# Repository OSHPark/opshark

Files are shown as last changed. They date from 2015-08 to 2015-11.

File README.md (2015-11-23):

# LAN'd Shark Project
The LAN'd Shark is a small, wifi-connected shark robot with some wicked hair and underglow lights. This was built and designed by the Oshpark team for [PDX Mini-Maker Faire](https://www.omsi.edu/maker-faire-pdx) 2015. 

The shark communicates via an MQTT server, and has supplimental remote control boards that allow a direct interface. However, you could esily modify it for automated or automatic control. If you need a remote MQTT server, [data.sparkfun.com](https://data.sparkfun.com/) is simple and easy to use, or you can install your own with tools  such as [Mosquitto](http://mosquitto.org/).

## Project Status
### [BaseStation](basestation/)
The basestation is fully operational, and capable of reading up to 3 teensies, and transmitting data over a network to an MQTT server.

### [Controller](controller/)
The controller is fully operational in both hardware and code.

### [Shark Bot](sharkbot/)
The Shark Brains hardware is fully operational, and can drive several servo motors from an ESP2866. 

The chassis mechanics are still a bit undefined, and a bit erratic. However, the base board works great as a mounting platform for servo motors, and can be laser cut

The Arduino sketch is still in a bit of a mess, but can read incoming controller data and react. However, the Animation and ServoPlus libraries have some bugs and needs to be rewritten/updated in order for the shark to react correctly.

Here's a picture of the completed Sharkbot. 
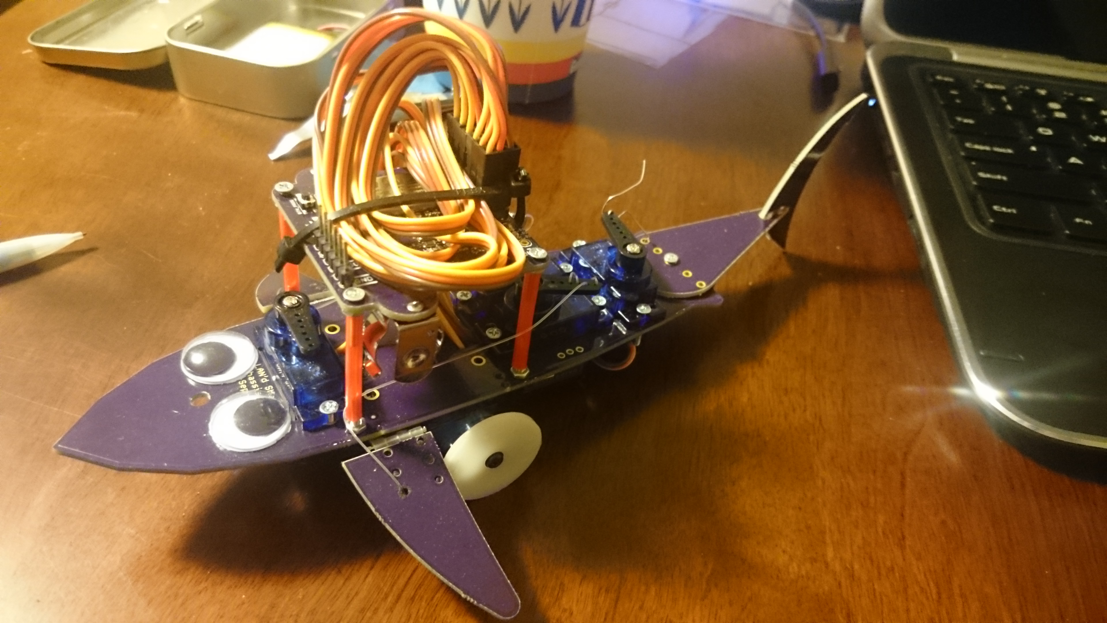
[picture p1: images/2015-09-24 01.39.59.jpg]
Shark posing


# Required Utilities
## Software
[Arduino 1.65](https://www.arduino.cc/en/Main/Software) 

[TeensyDuino](https://www.pjrc.com/teensy/td_download.html) if using the controllers

[ESP2866 Arduino](https://github.com/esp8266/Arduino) For the Sharkbot and basestation boards

[Eagle CAD](http://www.cadsoftusa.com/download-eagle/) is needed to modify the PCB files or generate gerbers. The `.BRD` files can be directly to [OSHPark.com](http://oshpark.com) for purchase without Eagle.

## Arduino Libraries
[PubSub Client](https://github.com/Imroy/pubsubclient)

[Teensy 3.1 SPI Slave library](https://github.com/soerup/Teensy-3.0-SPI-Master---Slave) for the controller boards

[Adafruit Neopixel (Teensy version)](https://github.com/PaulStoffregen/Adafruit_NeoPixel)

# Liscence 
Released currently under the [MIT License](./LICENSE.txt)

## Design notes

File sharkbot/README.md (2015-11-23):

# Sharkbot
This set of boards forms the mechanics of the roving LAN'd shark. It can be controlled via an MQTT server such as [Data.SparkFun.com](data.sparkfun.com), with either computer driven code or the companion [Controller](../controller/) and [BaseStation](../basestation/) boards. 

## Brains
This top board is the primary electronics, including the ESP chip and supporting programming components, voltage regulator, and LIPO battery monitoring. Also contains an output for a strand of Adafruit Neopixels

This board is entirely usable as a standalone servo controller. 
 
## Chassis and Fins
These boards contain the mechanics for sharklike actuation. The Chassis contains a strip of Neopixels for maximum gleefullness. 

If you don't need the neopixels, these boards can be exported as DXF or SVG and imported into most laser cutters or CNC software

# Software
This code uses the [ESP8266 Arduino](https://github.com/esp8266/Arduino) platform for the codebase. It also uses the Adafruit Neopixel library, which is conveniently included with the ESP Arduino downloads.

# Hardware

A very helpful resource was this tutorial for [creating a shark in maya](http://cgi.tutsplus.com/tutorials/create-a-realistic-shark-in-maya-using-subdivision-surfaces-part-3--cg-31246), even though I only used the 2d outline. 

The images in [references](./references) are copied from the tutorial for practical inclusion with the source files, and no claims are made to ownership. 

## BOM
See [BOM.txt](./BOM.txt) for the full component list from Eagle. Here's the notable/major components: 

- [ESP12E](https://www.adafruit.com/products/2491)
- Brains PCB. 
- Either Fin and Chassis  PCBs, or laser-cut equivilents (will have no place to mount neopixels)
- [Pair of AA Sized Lipo battery](https://www.sparkfun.com/products/7949)
- [MCP73871 LIPO battery management IC](http://www.digikey.com/product-detail/en/MCP73871-2CCI%2FML/MCP73871-2CCI%2FML-ND/1680971)
- [MC1703T 3.0V SOT23 Voltage ](http://www.digikey.com/product-detail/en/MCP1703T-3002E%2FCB/MCP1703T-3002E%2FCBCT-ND/1776944)
- [5x Neopixel LEDs](https://www.adafruit.com/products/1655)
- [5x Micro servos](http://www.hobbyking.com/hobbyking/store/__662__HXT900_Micro_Servo_1_6kg_0_12sec_9g.html). Various sizes and suppliers
- Several 2mm mounting screws, 3-6mm in length 
- 2mm nuts
- 2mm bolts
- Various passives and headers
- [Small nylon hinges](http://www.amazon.com/Du-Bro-Small-Nylon-Hinge-15-Pack/dp/B0006O4FYC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)

All passives use a universal footprint optimized for 0603, but tolerant of 0402 and 0805 components. 

# Errata/issues
The mechanics are not 100% defined, and some glue/creativity may be required to get this design fully operating. Our demo models were assembled with hot glue and some coffee stir sticks from 711.

There is no "off" button, which makes battery access critical as it's the only way to de-power the servo. The code implements a "sleep" function when the bootloader button is pressed, but this does not power down the servo motors.

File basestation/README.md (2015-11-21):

# BaseStation
This is an ESP2866 board that reads data from three [Teensy-based capacitive controllers](../controller/), and then sends it over wifi to an MQTT server to control a [shark bot](../sharkbot/).

## Simplified Wiring Schematic
Wiring the SPI bus requires 4 connections between the ESP and Teensy. 

```
  Controller                             BaseStation
  (Teensy 3.x)                           (ESP2866-12E)   
+--------------+                      +---------------+
|              |                      |               |
|           10 <------< CS <----------< Any IO        |
|              |                      |               |
|              |                      |               |
|           13 <------< SCK <---------< 14            |
|              |                      |               |
|              |                      |               |
|           11 >------> MISO >--------> 12            |
|              |                      |               |
|              |                      |               |
|           12 <------< MOSI <--------< 13            |
|              |                      |               |
+--------------+                      +---------------+
```

Other connections are simply there as part of the bootloading process.

# Known issues
Doesn't contain programming header of any sort, which makes changing wifi connections very difficult. Uploading firmware will require soldering to the ESP pads. 

It should be possible to configure the Base Station as a Wifi access point and run the MQTT server locally, in addition to handling the button input. However, this was not due due to time constraints and libraries available. 

# BOM
Only requires a few passive pull up/pull down resistors and an [ESP12E](https://www.adafruit.com/products/2491)

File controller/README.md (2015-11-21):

# Capacitive controller
This is a small Teensy 3.1 based board, which works as a 4 way direction pad with 2 buttons. The board provides a SPI interface, and the button presses can be picked up using a standard SPI Library.

# Usage 
Currently, this code only works when wired the BaseStation board. However, the Teensy is capable of operating as a USB human interface device, and with some tweaks to the code, the board can easily be used to operate a computer with capacitive buttons.

## Code requirements
Compiling the provided code requires a special [Teensy 3.1 SPI Slave library](https://github.com/soerup/Teensy-3.0-SPI-Master---Slave), as this functionality isn't provided by standard Arduino SPI libraries.

# BOM

- 1x [Teensy 3.x](https://www.pjrc.com/teensy/index.html). We're partial to the [purple ones](http://store.oshpark.com/products/teensy-3-1).
- 2x 14-pin male 0.1" headers
- 2x 14-pin female 0.1" headers

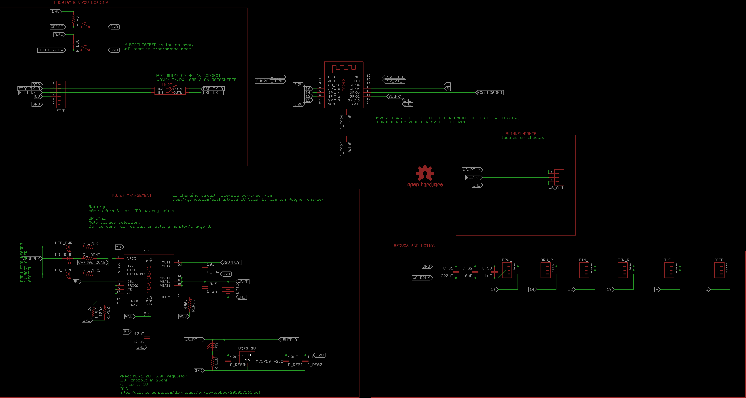
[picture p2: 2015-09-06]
sharkbot/eagle-files/brains.schematic.png

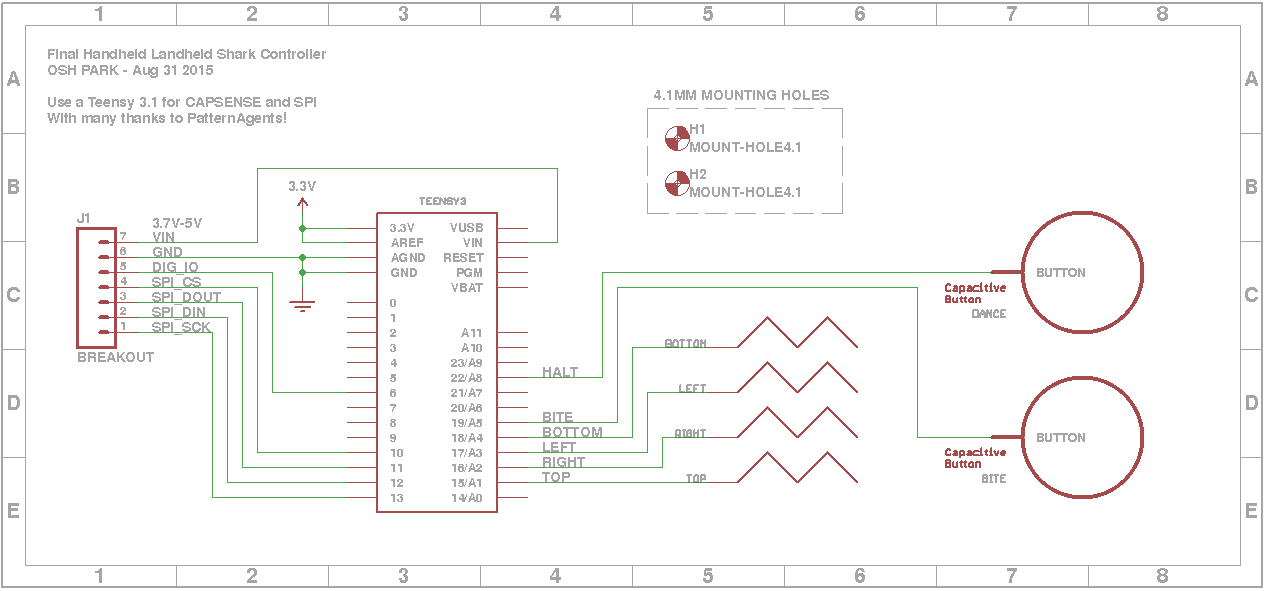
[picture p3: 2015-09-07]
controller/eagle-files/v3-schematic.png

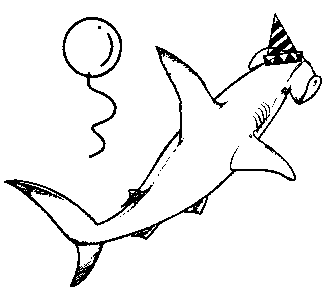
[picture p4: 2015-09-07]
controller/eagle-files/images/dance.bmp

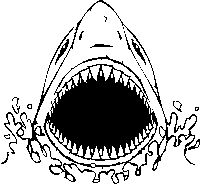
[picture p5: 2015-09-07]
controller/eagle-files/images/shark.bmp

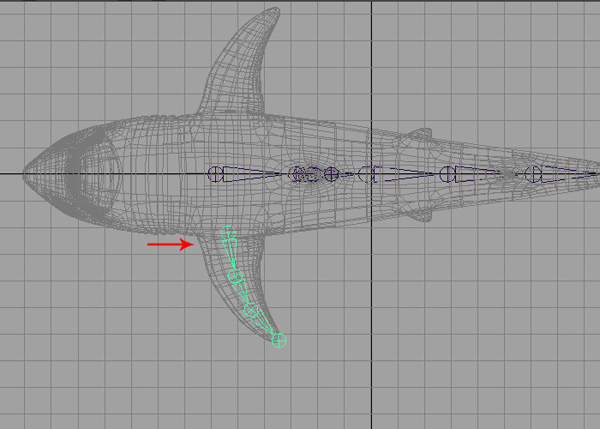
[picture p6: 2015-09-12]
sharkbot/references/Maya_Shark_PT3_11.jpg

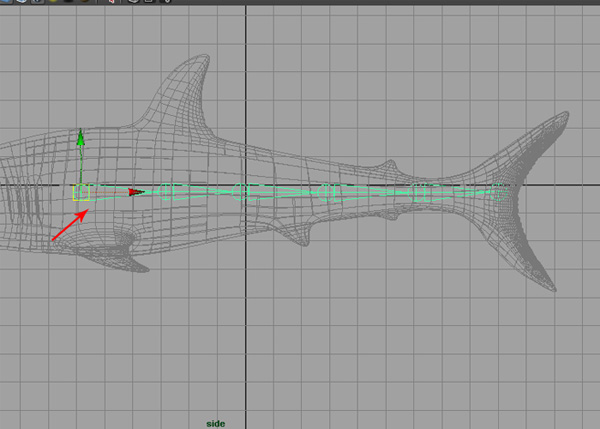
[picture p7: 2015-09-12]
sharkbot/references/Maya_Shark_PT3_6.jpg

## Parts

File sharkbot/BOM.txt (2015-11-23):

Partlist

Exported from brains.brd at 11/20/15 8:29 PM

EAGLE Version 7.3.0 Copyright (c) 1988-2015 CadSoft

Assembly variant: 

Part     Value             Package                  Library                    Position (mil)        Orientation

BAT2                       BATTERY-AA               SparkFun-Electromechanical (1000 1050)           MR270
BITE                       1X03_LOCK                SparkFun-Connectors        (1950 1420)           R0
BTN_PROG BUTTONPJRC        KMR432GLFS               tekdemo                    (740 1560)            R270
BTN_RST  BUTTONPJRC        KMR432GLFS               tekdemo                    (740 1200)            R270
C_5V     10uF              0402-0603-0805-UNIVERSAL tekdemo                    (1170 390)            R270
C_BAT    10uF              0402-0603-0805-UNIVERSAL tekdemo                    (1000 510)            R0
C_ESP1   1uF               0402-0603-0805-UNIVERSAL tekdemo                    (1880 1980)           R0
C_ESP2   0.1uF             0402-0603-0805-UNIVERSAL tekdemo                    (1880 2070)           R0
C_REG1   10uF              0402-0603-0805-UNIVERSAL tekdemo                    (1780 880)            R180
C_REG2   1uF               0402-0603-0805-UNIVERSAL tekdemo                    (1780 790)            R180
C_REGIN  10uF              0402-0603-0805-UNIVERSAL tekdemo                    (1780 570)            R0
C_S1     220uF             1210                     tekdemo                    (2090 750)            R180
C_S2     10uF              0402-0603-0805-UNIVERSAL tekdemo                    (2090 660)            R0
C_S3     .1uF              0402-0603-0805-UNIVERSAL tekdemo                    (2090 590)            R0
C_SUP    10uF              0402-0603-0805-UNIVERSAL tekdemo                    (1280 390)            R270
DRV_L                      1X03_LOCK                SparkFun-Connectors        (1950 890)            R0
DRV_R                      1X03_LOCK                SparkFun-Connectors        (1950 990)            R0
FIN_L                      1X03_LOCK                SparkFun-Connectors        (1950 1090)           R0
FIN_R                      1X03_LOCK                SparkFun-Connectors        (1950 1220)           R0
FTDI                       1X06_LOCK                SparkFun-Connectors        (660 970)             R270
IC_LIPO  MCP73871          QFN20                    adafruit                   (1180 630)            R180
LED                        0402-0603-0805-UNIVERSAL tekdemo                    (1490 390)            R270
LED_CHRG                   0402-0603-0805-UNIVERSAL tekdemo                    (1590 810)            R180
LED_DONE                   0402-0603-0805-UNIVERSAL tekdemo                    (1590 720)            R180
LED_PWR                    0402-0603-0805-UNIVERSAL tekdemo                    (1590 630)            R180
R_BOOT                     0402-0603-0805-UNIVERSAL tekdemo                    (950 880)             R180
R_LCHRG                    0402-0603-0805-UNIVERSAL tekdemo                    (1420 810)            R180
R_LDONE                    0402-0603-0805-UNIVERSAL tekdemo                    (1420 720)            R180
R_LED                      0402-0603-0805-UNIVERSAL tekdemo                    (1390 390)            R270
R_LPWR                     0402-0603-0805-UNIVERSAL tekdemo                    (1420 630)            R180
R_PD1    2k                0402-0603-0805-UNIVERSAL tekdemo                    (950 690)             R180
R_PD2    100k              0402-0603-0805-UNIVERSAL tekdemo                    (950 780)             R180
R_PD3    150k              0402-0603-0805-UNIVERSAL tekdemo                    (1420 900)            R0
R_RST                      0402-0603-0805-UNIVERSAL tekdemo                    (950 960)             R180
TAIL                       1X03_LOCK                SparkFun-Connectors        (1950 1320)           R0
UART_X   UART_SWITCHER0603 UART_SWITCHER_0603       tekdemo                    (1300 1400)           MR270
VREG_3V  MC1703T-3v0       SOT23                    tekdemo                    (1780 680)            R90
WS_OUT                     1X03_LOCK                SparkFun-Connectors        (1950 500)            R0
X1                         ESP-12                   adafruit                   (1360 1370)           R90

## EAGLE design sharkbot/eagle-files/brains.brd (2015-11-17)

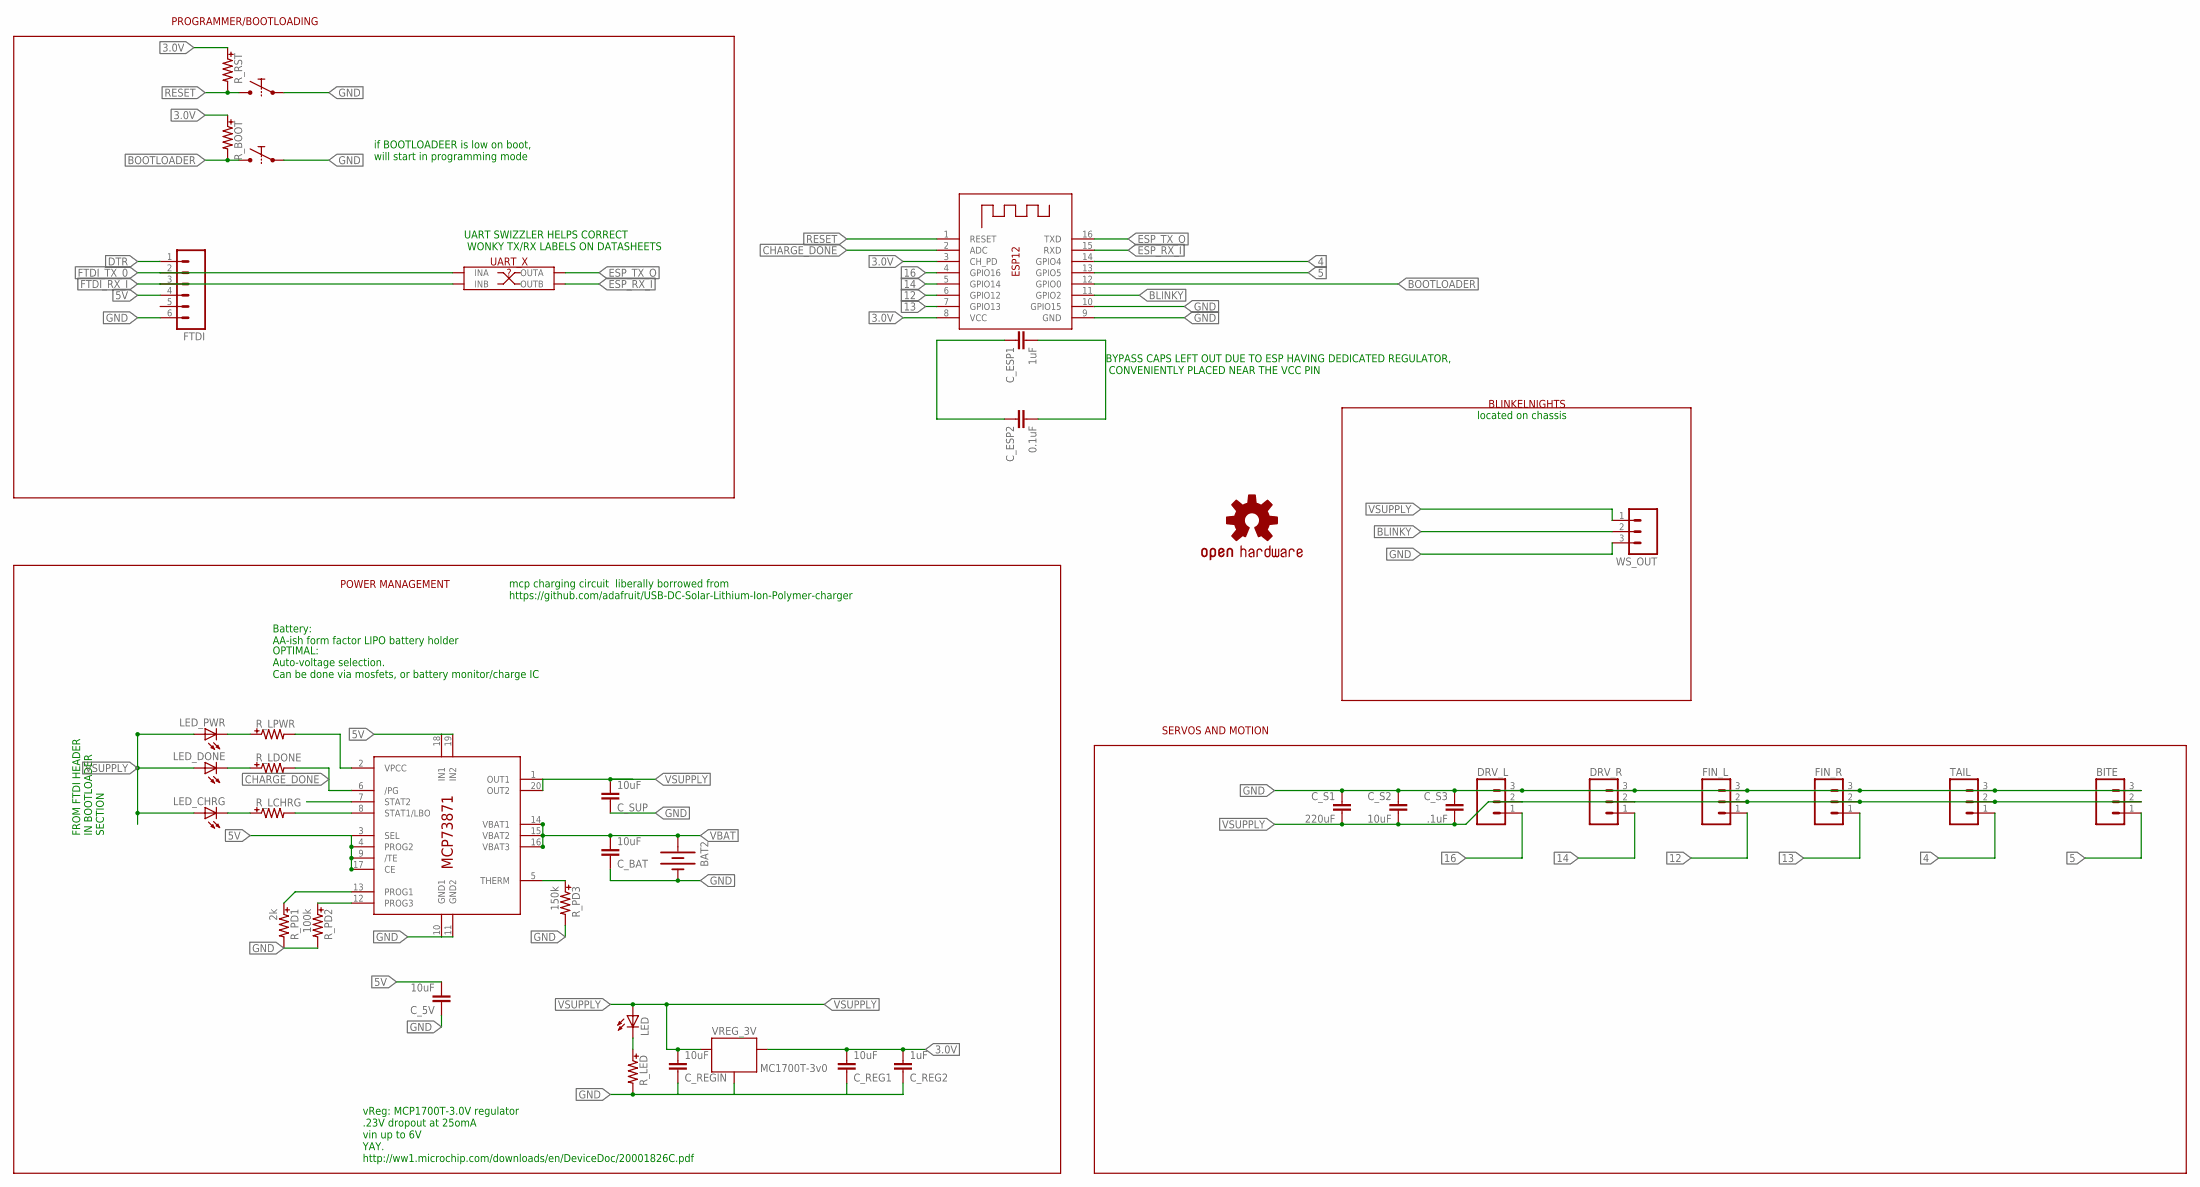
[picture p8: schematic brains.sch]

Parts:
BAT2: BATTERYAA; BATTERY-AA
BITE: M03LOCK; 1X03_LOCK
BTN_PROG: BUTTONPJRC; BUTTON-PJRC
BTN_RST: BUTTONPJRC; BUTTON-PJRC
C_5V: 10uF; 0402-0603-0805-UNIVERSAL
C_BAT: 10uF; 0402-0603-0805-UNIVERSAL
C_ESP1: 1uF; 0402-0603-0805-UNIVERSAL
C_ESP2: 0.1uF; 0402-0603-0805-UNIVERSAL
C_REG1: 10uF; 0402-0603-0805-UNIVERSAL
C_REG2: 1uF; 0402-0603-0805-UNIVERSAL
C_REGIN: 10uF; 0402-0603-0805-UNIVERSAL
C_S1: 220uF; 1210
C_S2: 10uF; 0402-0603-0805-UNIVERSAL
C_S3: .1uF; 0402-0603-0805-UNIVERSAL
C_SUP: 10uF; 0402-0603-0805-UNIVERSAL
DRV_L: M03LOCK; 1X03_LOCK
DRV_R: M03LOCK; 1X03_LOCK
FIN_L: M03LOCK; 1X03_LOCK
FIN_R: M03LOCK; 1X03_LOCK
FTDI: M06LOCK; 1X06_LOCK
IC_LIPO: MCP73871; QFN20
LED: LEDUNIVERSAL; 0402-0603-0805-UNIVERSAL
LED_CHRG: LEDUNIVERSAL; 0402-0603-0805-UNIVERSAL
LED_DONE: LEDUNIVERSAL; 0402-0603-0805-UNIVERSAL
LED_PWR: LEDUNIVERSAL; 0402-0603-0805-UNIVERSAL
LOGO1: OSHW-LOGOS; OSHW-LOGO-S
R_BOOT: RESISTORUNIVERSAL; 0402-0603-0805-UNIVERSAL
R_LCHRG: RESISTORUNIVERSAL; 0402-0603-0805-UNIVERSAL
R_LDONE: RESISTORUNIVERSAL; 0402-0603-0805-UNIVERSAL
R_LED: RESISTORUNIVERSAL; 0402-0603-0805-UNIVERSAL
R_LPWR: RESISTORUNIVERSAL; 0402-0603-0805-UNIVERSAL
R_PD1: 2k; 0402-0603-0805-UNIVERSAL
R_PD2: 100k; 0402-0603-0805-UNIVERSAL
R_PD3: 150k; 0402-0603-0805-UNIVERSAL
R_RST: RESISTORUNIVERSAL; 0402-0603-0805-UNIVERSAL
TAIL: M03LOCK; 1X03_LOCK
UART_X: UART_SWITCHER0603; UART_SWITCHER_0603
VREG_3V: MC1700T-3v0; SOT23
WS_OUT: M03LOCK; 1X03_LOCK
X1: ESP-12

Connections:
3.0V: C_REG1.+ (2), C_REG2.+ (2), R_BOOT.+ (1), R_RST.+ (1), VREG_3V.2 (OUT), X1.3 (CH_PD), X1.8 (VCC)
4: TAIL.1, X1.14 (GPIO4)
5: BITE.1, X1.13 (GPIO5)
5V: C_5V.+ (2), FTDI.4, IC_LIPO.3 (SEL), IC_LIPO.4 (PROG2), IC_LIPO.9 (/TE), IC_LIPO.17 (CE), IC_LIPO.18 (IN1), IC_LIPO.19 (IN2)
12: FIN_L.1, X1.6 (GPIO12)
13: FIN_R.1, X1.7 (GPIO13)
14: DRV_R.1, X1.5 (GPIO14)
16: DRV_L.1, X1.4 (GPIO16)
BLINKY: WS_OUT.2, X1.11 (GPIO2)
BOOTLOADER: BTN_PROG.A1, BTN_PROG.A2, R_BOOT.- (2), X1.12 (GPIO0)
CHARGE_DONE: IC_LIPO.6 (/PG), R_LDONE.- (2), X1.2 (ADC)
DTR: FTDI.1
ESP_RX_I: UART_X.TX_B (OUTB), X1.15 (RXD)
ESP_TX_O: UART_X.RX_B (OUTA), X1.16 (TXD)
FTDI_RX_I: FTDI.3, UART_X.RX_A (INB)
FTDI_TX_0: FTDI.2, UART_X.TX_A (INA)
GND: BAT2.GND@1 (-), BITE.3, BTN_PROG.B1, BTN_PROG.B2, BTN_RST.B1, BTN_RST.B2, C_5V.- (1), C_BAT.- (1), C_REG1.- (1), C_REG2.- (1), C_REGIN.- (1), C_S1.1, C_S2.- (1), C_S3.- (1), C_SUP.- (1), DRV_L.3, DRV_R.3, FIN_L.3, FIN_R.3, FTDI.6, IC_LIPO.10 (GND1), IC_LIPO.11 (GND2), R_LED.- (2), R_PD1.- (2), R_PD2.- (2), R_PD3.- (2), TAIL.3, VREG_3V.1 (GND), WS_OUT.3, X1.9 (GND), X1.10 (GPIO15)
unnamed: IC_LIPO.8 (STAT1/LBO), R_LCHRG.- (2)
unnamed: C_ESP1.- (1), C_ESP2.- (1)
unnamed: IC_LIPO.5 (THERM), R_PD3.+ (1)
unnamed: LED_CHRG.- (C), R_LCHRG.+ (1)
unnamed: LED.- (C), R_LED.+ (1)
unnamed: LED_DONE.- (C), R_LDONE.+ (1)
unnamed: LED_PWR.- (C), R_LPWR.+ (1)
unnamed: IC_LIPO.2 (VPCC), R_LPWR.- (2)
unnamed: C_ESP1.+ (2), C_ESP2.+ (2)
unnamed: IC_LIPO.12 (PROG3), R_PD2.+ (1)
unnamed: IC_LIPO.13 (PROG1), R_PD1.+ (1)
RESET: BTN_RST.A1, BTN_RST.A2, R_RST.- (2), X1.1 (RESET)
VBAT: BAT2.PWR@1 (+), C_BAT.+ (2), IC_LIPO.14 (VBAT1), IC_LIPO.15 (VBAT2), IC_LIPO.16 (VBAT3)
VSUPPLY: BITE.2, C_REGIN.+ (2), C_S1.2, C_S2.+ (2), C_S3.+ (2), C_SUP.+ (2), DRV_L.2, DRV_R.2, FIN_L.2, FIN_R.2, IC_LIPO.1 (OUT1), IC_LIPO.20 (OUT2), LED.+ (A), LED_CHRG.+ (A), LED_DONE.+ (A), LED_PWR.+ (A), TAIL.2, VREG_3V.3 (IN), WS_OUT.1

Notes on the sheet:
if BOOTLOADEER is low on boot, will start in programming mode
PROGRAMMER/BOOTLOADING
POWER MANAGEMENT
SERVOS AND MOTION
BLINKELNIGHTS
OPTIMAL: Auto-voltage selection. Can be done via mosfets, or battery monitor/charge IC
Battery: AA-ish form factor LIPO battery holder
UART SWIZZLER HELPS CORRECT WONKY TX/RX LABELS ON DATASHEETS
vReg: MCP1700T-3.0V regulator .23V dropout at 25omA vin up to 6V YAY. http://ww1.microchip.com/downloads/en/DeviceDoc/20001826C.pdf
mcp charging circuit liberally borrowed from https://github.com/adafruit/USB-DC-Solar-Lithium-Ion-Polymer-charger
FROM FTDI HEADER IN BOOTLOADER SECTION
located on chassis
BYPASS CAPS LEFT OUT DUE TO ESP HAVING DEDICATED REGULATOR, CONVENIENTLY PLACED NEAR THE VCC PIN

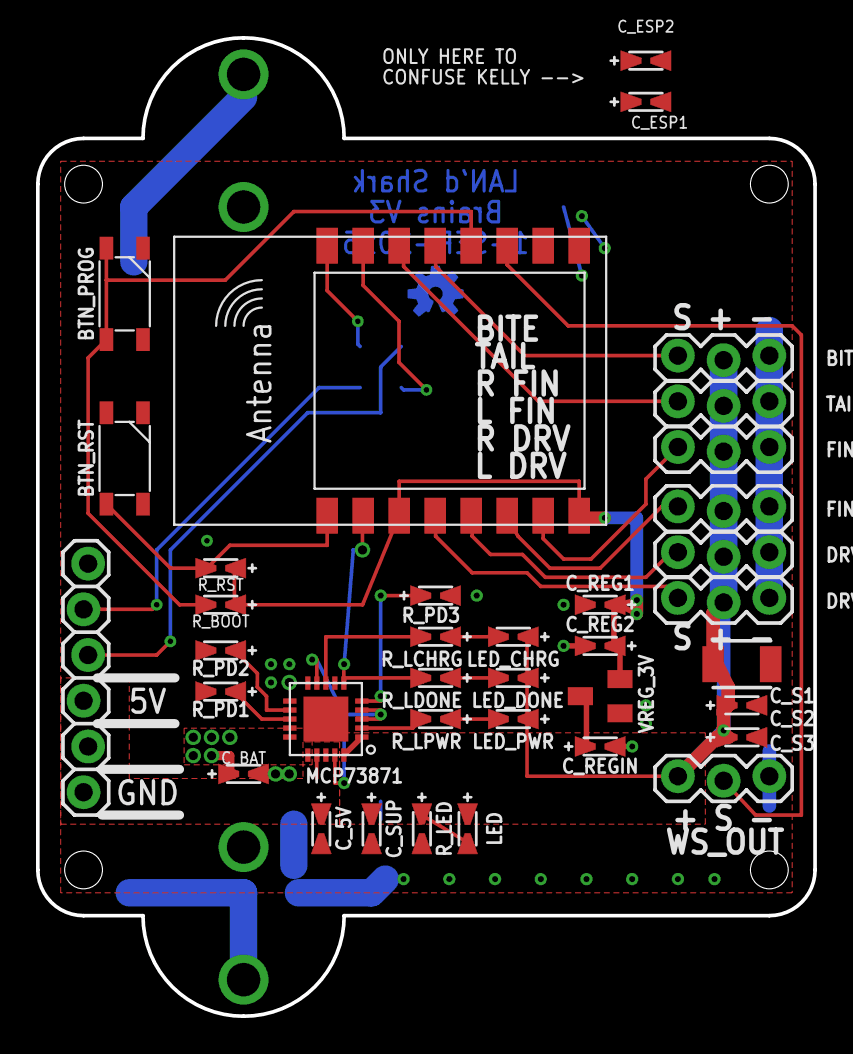
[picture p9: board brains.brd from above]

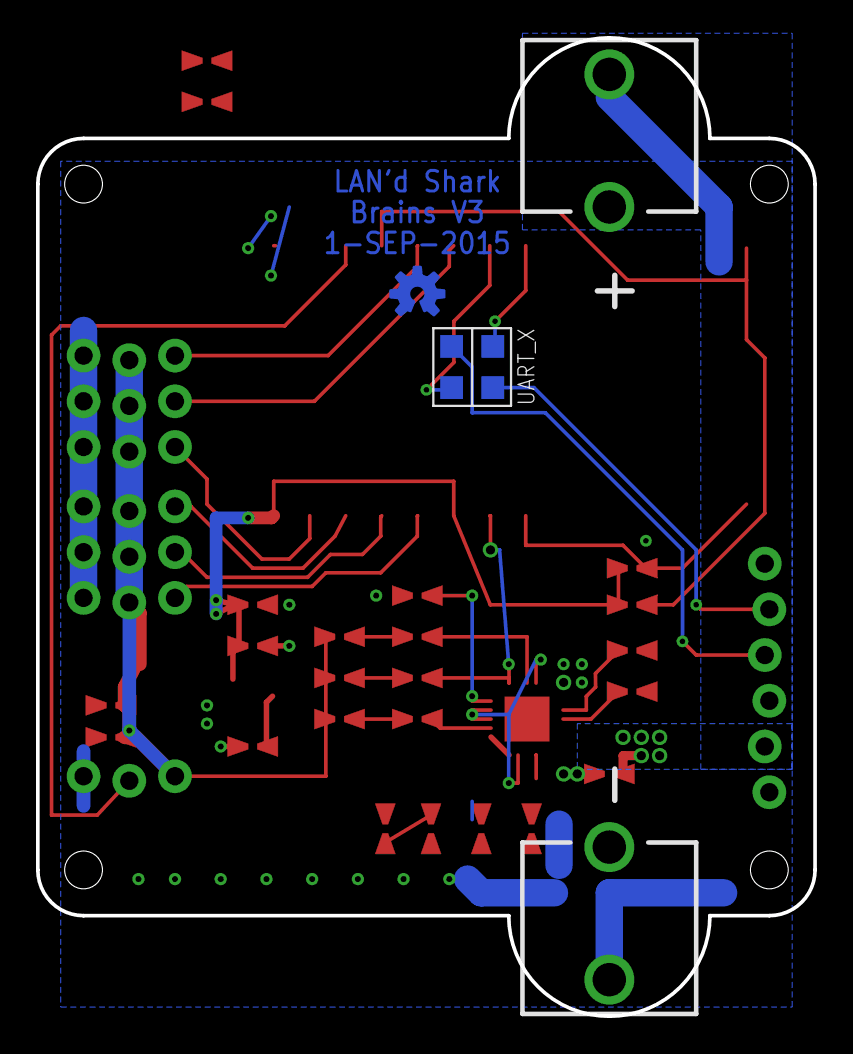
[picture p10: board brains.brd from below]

Board: 2 copper layers, 43.2 x 54.4 mm, 40 parts (3 on the bottom side), 30 nets.

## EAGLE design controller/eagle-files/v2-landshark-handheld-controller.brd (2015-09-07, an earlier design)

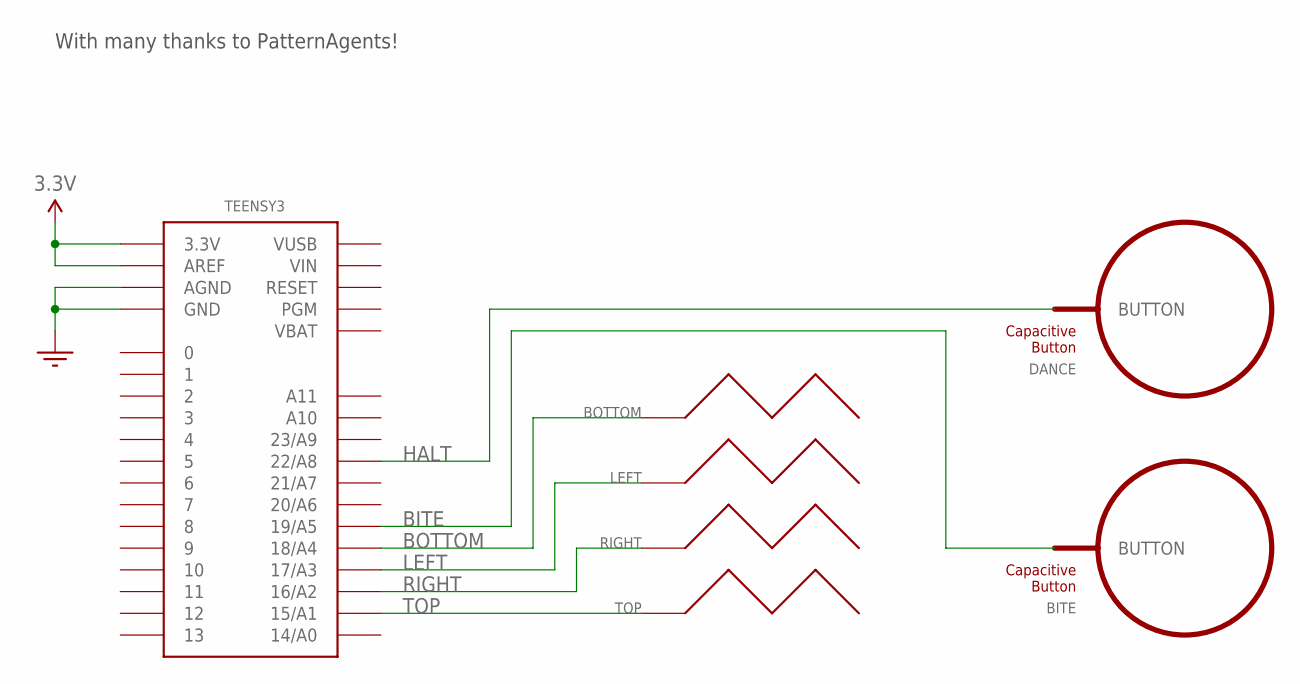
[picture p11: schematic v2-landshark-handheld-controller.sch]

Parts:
BITE: BUTTON_PASSIVE_12MM_BITE
BOTTOM: SLIDER_PASSIVE_1SEG; SLIDER_PASSIVE_1SEG_12MM
DANCE: BUTTON_PASSIVE_12MM_DANCE
LEFT: SLIDER_PASSIVE_1SEG; SLIDER_PASSIVE_1SEG_12MM
RIGHT: SLIDER_PASSIVE_1SEG; SLIDER_PASSIVE_1SEG_12MM
TEENSY3: TEENSY_3.0+4
TOP: SLIDER_PASSIVE_1SEG; SLIDER_PASSIVE_1SEG_12MM

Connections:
3.3V: TEENSY3.3.3V, TEENSY3.3.3V1 (3.3V), TEENSY3.AREF
BITE: BITE.BUTTON, TEENSY3.19/A5
BOTTOM: BOTTOM.P$1, TEENSY3.18/A4
GND: TEENSY3.AGND, TEENSY3.GND, TEENSY3.GND1 (GND)
HALT: DANCE.BUTTON, TEENSY3.22/A8
LEFT: LEFT.P$1, TEENSY3.17/A3
RIGHT: RIGHT.P$1, TEENSY3.16/A2
TOP: TEENSY3.15/A1, TOP.P$1
VBAT: TEENSY3.VBAT
VIN: TEENSY3.VIN
VUSB: TEENSY3.VUSB

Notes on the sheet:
With many thanks to PatternAgents!

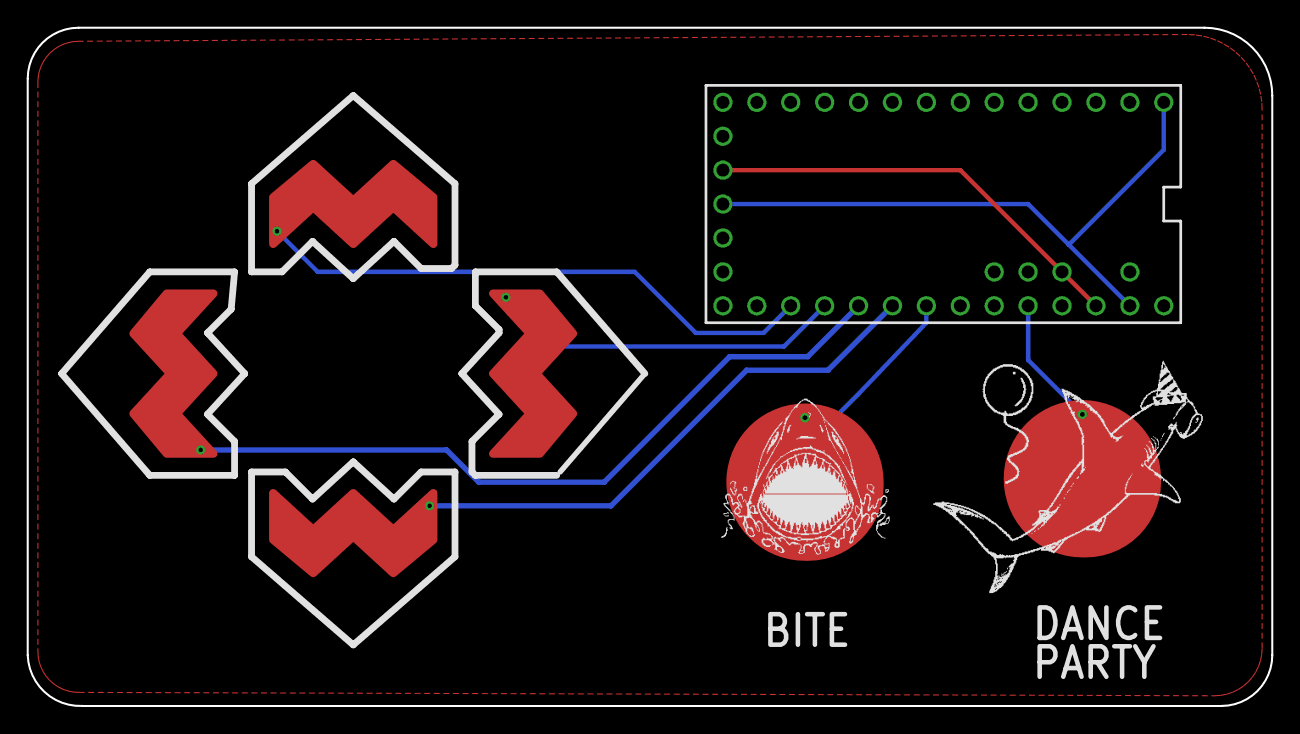
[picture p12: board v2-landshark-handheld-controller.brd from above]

Board: 2 copper layers, 93.2 x 50.8 mm, 7 parts (0 on the bottom side), 8 nets.

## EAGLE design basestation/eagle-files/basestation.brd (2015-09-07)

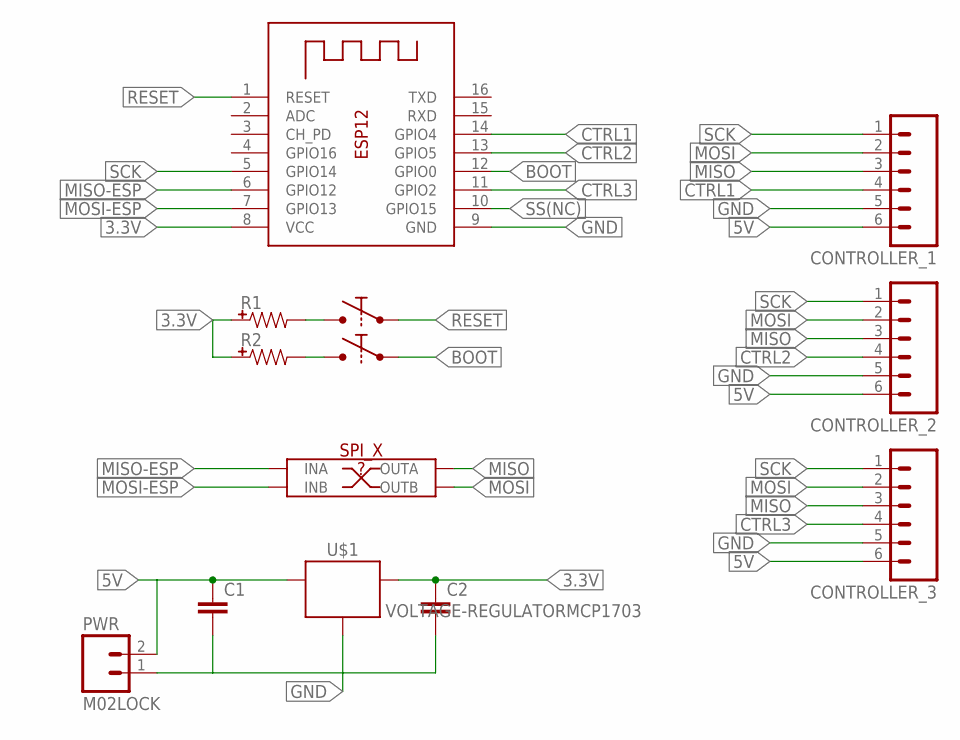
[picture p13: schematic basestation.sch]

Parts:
BOOT: BUTTONPJRC; BUTTON-PJRC
C1, C2: CAPUNIVERSAL; 0402-0603-0805-UNIVERSAL
CONTROLLER_1, CONTROLLER_2, CONTROLLER_3: M06LOCK; 1X06_LOCK
PWR: M02LOCK; 1X02_LOCK
R1, R2: RESISTORUNIVERSAL; 0402-0603-0805-UNIVERSAL
RESET: BUTTONPJRC; BUTTON-PJRC
SPI_X: UART_SWITCHER0603; UART_SWITCHER_0603
U$1: VOLTAGE-REGULATORMCP1703; SOT23
X1: ESP-12

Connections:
3.3V: C2.- (1), R1.- (1), R2.- (1), U$1.2 (OUT), X1.8 (VCC)
5V: C1.- (1), CONTROLLER_1.6, CONTROLLER_2.6, CONTROLLER_3.6, PWR.2, U$1.3 (IN)
BOOT: BOOT.B1, BOOT.B2, X1.12 (GPIO0)
CTRL1: CONTROLLER_1.4, X1.14 (GPIO4)
CTRL2: CONTROLLER_2.4, X1.13 (GPIO5)
CTRL3: CONTROLLER_3.4, X1.11 (GPIO2)
GND: C1.+ (2), C2.+ (2), CONTROLLER_1.5, CONTROLLER_2.5, CONTROLLER_3.5, PWR.1, U$1.1 (GND), X1.9 (GND)
MISO: CONTROLLER_1.3, CONTROLLER_2.3, CONTROLLER_3.3, SPI_X.RX_B (OUTA)
MISO-ESP: SPI_X.TX_A (INA), X1.6 (GPIO12)
MOSI: CONTROLLER_1.2, CONTROLLER_2.2, CONTROLLER_3.2, SPI_X.TX_B (OUTB)
MOSI-ESP: SPI_X.RX_A (INB), X1.7 (GPIO13)
unnamed: R1.+ (2), RESET.A1, RESET.A2
unnamed: BOOT.A1, BOOT.A2, R2.+ (2)
RESET: RESET.B1, RESET.B2, X1.1 (RESET)
SCK: CONTROLLER_1.1, CONTROLLER_2.1, CONTROLLER_3.1, X1.5 (GPIO14)
SS(NC): X1.10 (GPIO15)

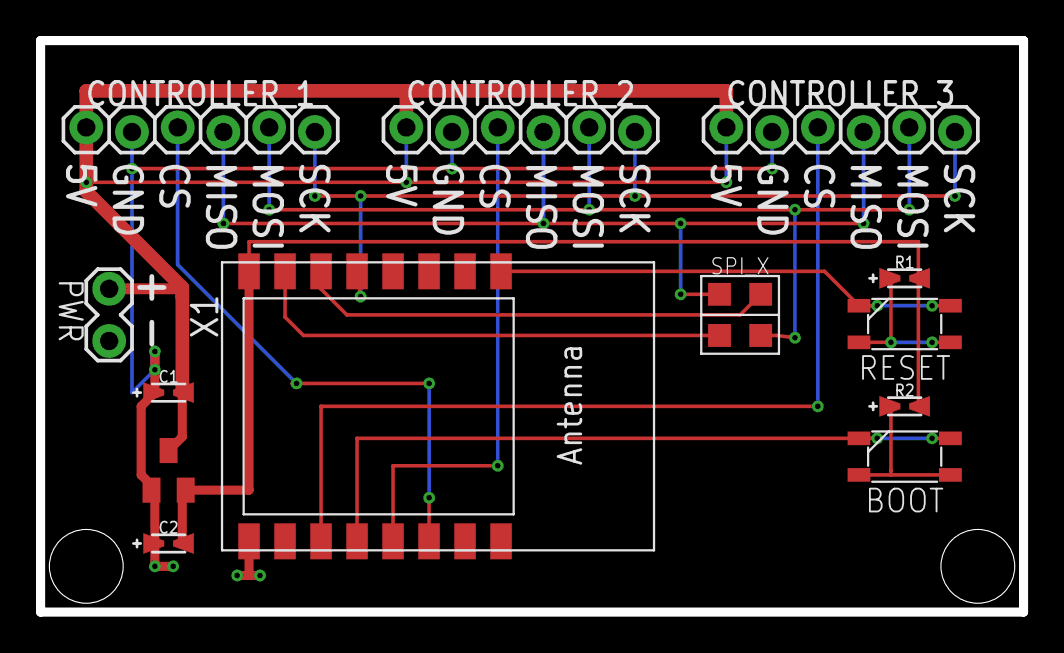
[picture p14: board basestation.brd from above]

Board: 2 copper layers, 54.6 x 31.8 mm, 13 parts (0 on the bottom side), 15 nets.

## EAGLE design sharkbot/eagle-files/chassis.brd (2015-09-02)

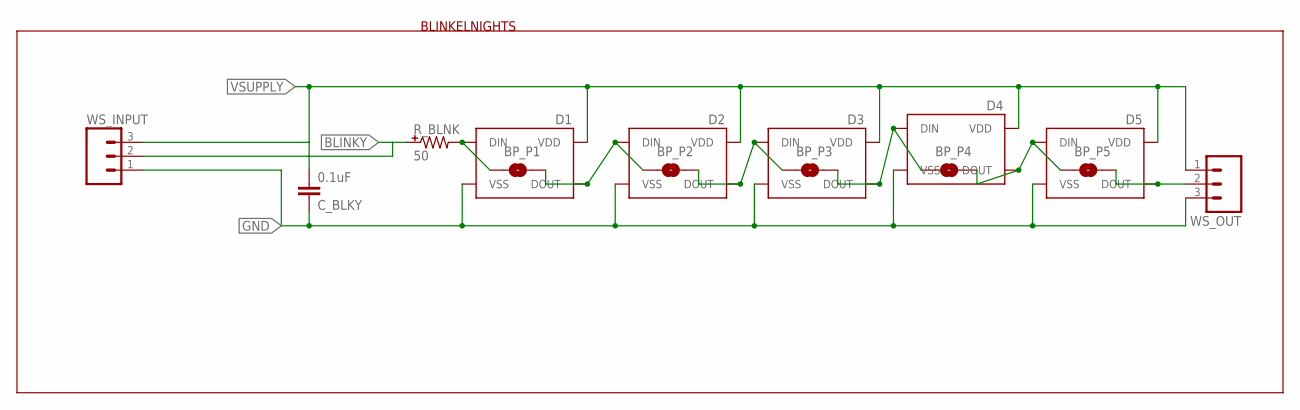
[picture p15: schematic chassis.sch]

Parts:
BP_P1, BP_P2, BP_P3, BP_P4, BP_P5: JUMPER-PAD-2-NOYES_SILK; PAD-JUMPER-2-NO_YES_SILK
C_BLKY: 0.1uF; 0402-0603-0805-UNIVERSAL
D1, D2, D3, D4, D5: WS2812B
R_BLNK: 50; 0402-0603-0805-UNIVERSAL
WS_INPUT: M03LOCK; 1X03_LOCK
WS_OUT: M03LOCK; 1X03_LOCK

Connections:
BLINKY: R_BLNK.- (1), WS_INPUT.2
GND: C_BLKY.- (1), D1.3 (VSS), D2.3 (VSS), D3.3 (VSS), D4.3 (VSS), D5.3 (VSS), WS_INPUT.1, WS_OUT.3
unnamed: BP_P1.2, BP_P2.1, D1.2 (DOUT), D2.4 (DIN)
unnamed: BP_P4.2, BP_P5.1, D4.2 (DOUT), D5.4 (DIN)
unnamed: BP_P5.2, D5.2 (DOUT), WS_OUT.2
unnamed: BP_P1.1, D1.4 (DIN), R_BLNK.+ (2)
unnamed: BP_P2.2, BP_P3.1, D2.2 (DOUT), D3.4 (DIN)
unnamed: BP_P3.2, BP_P4.1, D3.2 (DOUT), D4.4 (DIN)
VSUPPLY: C_BLKY.+ (2), D1.1 (VDD), D2.1 (VDD), D3.1 (VDD), D4.1 (VDD), D5.1 (VDD), WS_INPUT.3, WS_OUT.1

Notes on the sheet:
BLINKELNIGHTS

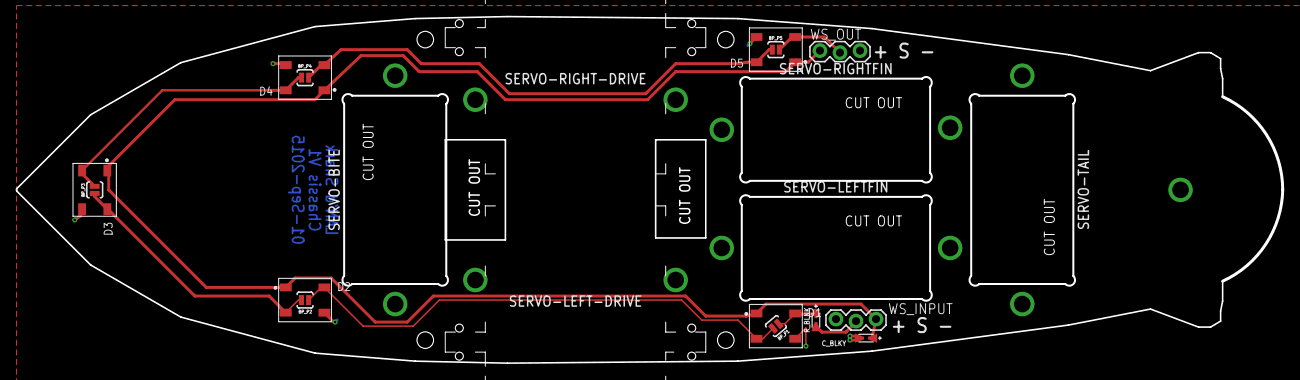
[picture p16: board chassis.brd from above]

Board: 2 copper layers, 160.5 x 43.9 mm, 20 parts (0 on the bottom side), 9 nets.

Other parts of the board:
SERVO-BITE: MICROSERVER-VERTICAL
SERVO-LEFT-DRIVE: RIGHT-DRIVE-SERVO; MICROSERVO-HORIZONTAL-FLIPPED
SERVO-LEFTFIN: MICROSERVER-VERTICAL
SERVO-RIGHT-DRIVE: MICROSERVO-HORIZONTAL
SERVO-RIGHTFIN: MICROSERVER-VERTICAL
SERVO-TAIL: MICROSERVER-VERTICAL

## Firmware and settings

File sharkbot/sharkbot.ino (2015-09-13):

/*
 Basic MQTT example

  - connects to an MQTT server
  - publishes "hello world" to the topic "outTopic"
  - subscribes to the topic "inTopic"

  AN IMPORTANT NOTE: This uses the PubSub library from
  https://github.com/Imroy/pubsubclient
*/

#include <ESP8266WiFi.h>
#include <PubSubClient.h>
#include <elapsedMillis.h>
#include <Streaming.h>
#include <Servo.h>
#include "RemoteController.h"
#include "SharkBot.h"

//const char *ssid =	"oshpark opsharks";		// cannot be longer than 32 characters!
//const char *pass =	"";		//

const char *ssid =	"HOME-1972";		// cannot be longer than 32 characters!
const char *pass =	"9BC5A011D3345830";		//

// Update these with values suitable for your network.
IPAddress server(10, 0, 0, 15);
WiFiClient wclient;
PubSubClient client(wclient, server);


//Set up a tiny remote instance to handle virtual buttons
RemoteController remote(1);


//Create our physical sharkbot
Sharkbot shark(1);


//Set up our input handling functions
void callback(const MQTT::Publish& pub) {
  // handle message arrived
  String msg = pub.payload_string();
  String topic = pub.topic();

  //Echo things out to serial
  Serial << "Recieved message in : " << pub.topic() << " :: " << msg << endl;

  //trip the last bit of the topic to get the button
  topic = topic.substring(topic.lastIndexOf('/') + 1);

  //The remote class will handle all of the button tracking.
  remote.setButton(topic, msg);
}

//Create our MQTT connection in advance to simplify things later
MQTT::Connect mqtt_connect = MQTT::Connect("landshark1")
                             .set_will("/landshark/1/status", "Shark 1 offline")
                             .set_keepalive(5);

MQTT::Subscribe mqtt_subs = MQTT::Subscribe("/landshark/1/input/+")
                            //.add_topic("/landshark/1/jabber");
                            ;

//Misc Variables
int retries = 0;
elapsedMillis heartbeat;

void setup()
{
  // Setup console
  Serial.begin(115200);
  delay(10);

  Serial << "Shark 1 cbooting " << endl;
  Serial << "Chip ID Number " << ESP.getChipId() << endl;

  client.set_callback(callback);


  //Ensure that we're connected to wifi
  while ((WiFi.status() != WL_CONNECTED)) {
    retries++;
    delay(500);
    Serial.print(".");
  }
  if (WiFi.status() == WL_CONNECTED) {
    Serial << "WiFi connected: took " << retries << " attempts" << endl;


    //Connect to MQTT server
    if (client.connect(mqtt_connect)) {
      Serial << "Shark 1 connected to MQTT" << endl;
      client.publish("/landshark/1/status", "Shark 1 online");
      client.subscribe(mqtt_subs);
    }

  }


}



void loop()
{

  //MQTT client loop structure
  client.loop();

  //maintain a heartbeat on serial and server, and reboot if we've totally lost wifi.
  if (WiFi.status() == WL_CONNECTED) {
    //Send a heartbeat
    if (heartbeat > 1000) {
      heartbeat = 0;
      String s = String(millis()) ;
      Serial << "Heartbeat: " << s << endl;
    }
  }
  else if (heartbeat > 12000) {
    Serial << "Lost Wifi: Restarting at time" << heartbeat << endl;
    ESP.reset();
  }

  //
  //Now, do some clever things with the shark! :D
  //

  //If no one is around, do something reasonable and/or cool.
  if (remote.isIdle()) {
    shark.idle();
  }
  else {
    shark.notidle();
    shark.manual(remote.controllerState());
  }


  //This updates any ongoing animations
  shark.update();


  if (digitalRead(0) == LOW) {
    shark.disable();
    while (1) {
      delay(200);
      ESP.deepSleep(5000, WAKE_RF_DEFAULT);
    }
  }
}

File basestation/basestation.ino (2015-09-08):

/*
This code handles reading the 3 controllers from the operator's station, and then transmits the results to an MQTT broker. 

From there, the controlled sharks will get the information, and respond approprately.
  
  AN IMPORTANT NOTE: This uses the PubSub library from 
  https://github.com/Imroy/pubsubclient
  This library has been updated to operate with the ESP2866, which is the target platform for this code
*/

#include <ESP8266WiFi.h>
#include <PubSubClient.h>
#include <elapsedMillis.h>
#include <Streaming.h>
#include "controller.h"
#include <SPI.h>


/*
  Configure wifi and MQTT Server
*/

const char *ssid =	"HOME-1972";		// cannot be longer than 32 characters!
const char *pass =	"9BC5A011D3345830";		//

// Update these with values suitable for your network.
IPAddress server(10, 0, 0, 15);

WiFiClient wclient;
PubSubClient client(wclient, server);



/*
  MQTT Recieve handling
*/

void callback(const MQTT::Publish& pub) {
  // handle message arrived
  Serial<<"Recieved message in : " << pub.topic() << " :: " << pub.payload_string() << endl;
}

/*
  Create instances for all the controllers
*/
SPIController controller1(1,4);
SPIController controller2(2,5);
SPIController controller3(3,2);


void setup()
{
  // Setup console
  Serial.begin(115200);
  delay(10);
  Serial.println();
  Serial.println();

  client.set_callback(callback);

  WiFi.begin(ssid, pass);

  int retries = 0;
  while ((WiFi.status() != WL_CONNECTED) && (retries < 10)) {
    retries++;
    delay(500);
    Serial.print(".");
  }
  if (WiFi.status() == WL_CONNECTED) {
    Serial.println("");
    Serial.println("WiFi connected");
  }

  if (client.connect("arduinoClient")) {
    Serial<<"Shark 1 connected to MQTT"<<endl;
    client.publish("/landshark/basestation", "Basestation online");
    client.subscribe("/landshark/+/status");
  }
}


elapsedMillis printer;

void loop()
{
  //Update the MQTT 
  client.loop();
  
  //grab new data from the controllers
  controller1.update();
  controller2.update();
  controller3.update();
  
  
  
  //update our shark with any relevant button updates
  if(controller1.upUpdated()){
    client.publish("/landshark/1/input/up",controller1.upPressed()?"true":"false");
  }
  if(controller1.downUpdated()){
    client.publish("/landshark/1/input/down",controller1.downPressed()?"true":"false");
  }
  if(controller1.leftUpdated()){
    client.publish("/landshark/1/input/left",controller1.leftPressed()?"true":"false");
  }
  if(controller1.rightUpdated()){
    client.publish("/landshark/1/input/right",controller1.rightPressed()?"true":"false");
  }
  if(controller1.biteUpdated()){
    client.publish("/landshark/1/input/bite",controller1.bitePressed()?"true":"false");
  }
  if(controller1.danceUpdated()){
    client.publish("/landshark/1/input/dance",controller1.dancePressed()?"true":"false");
  }
  
  
  //update our shark with any relevant button updates
  if(controller2.upUpdated()){
    client.publish("/landshark/2/input/up",controller2.upPressed()?"true":"false");
  }
  if(controller2.downUpdated()){
    client.publish("/landshark/2/input/down",controller2.downPressed()?"true":"false");
  }
  if(controller2.leftUpdated()){
    client.publish("/landshark/2/input/left",controller2.leftPressed()?"true":"false");
  }
  if(controller2.rightUpdated()){
    client.publish("/landshark/2/input/right",controller2.rightPressed()?"true":"false");
  }
  if(controller2.biteUpdated()){
    client.publish("/landshark/2/input/bite",controller2.bitePressed()?"true":"false");
  }
  if(controller2.danceUpdated()){
    client.publish("/landshark/2/input/dance",controller2.dancePressed()?"true":"false");
  }
  
  
    //update our shark with any relevant button updates
  if(controller3.upUpdated()){
    client.publish("/landshark/3/input/up",controller3.upPressed()?"true":"false");
  }
  if(controller3.downUpdated()){
    client.publish("/landshark/3/input/down",controller3.downPressed()?"true":"false");
  }
  if(controller3.leftUpdated()){
    client.publish("/landshark/3/input/left",controller3.leftPressed()?"true":"false");
  }
  if(controller3.rightUpdated()){
    client.publish("/landshark/3/input/right",controller3.rightPressed()?"true":"false");
  }
  if(controller3.biteUpdated()){
    client.publish("/landshark/3/input/bite",controller3.bitePressed()?"true":"false");
  }
  if(controller3.danceUpdated()){
    client.publish("/landshark/3/input/dance",controller3.dancePressed()?"true":"false");
  }
  

  
  
  

  //print some human readable things
  if (printer > 3000) {
    printer = 0;
    
    
    
    //int c=controller1.readByte();
    Serial.print("Controller status: ");
    //Serial.println(c);
    
    String s=String(millis()) ;
    client.publish("/landshark/1/status",s );

  }


}

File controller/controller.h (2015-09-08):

#ifndef CONTROLLER_H
#define CONTROLLER_H
#include <Arduino.h>

/** Bit positions for sending button data over SPI
 *  X X UP DOWN LEFT RIGHT BITE DANCE
 */
#define UP 		5
#define DOWN 	4
#define LEFT 	3
#define RIGHT 	2
#define BITE 	1
#define DANCE 	0

/** Write down the pin positions for our capacitive sense buttons
 */
#define pinUp    15
#define pinLeft  18
#define pinRight 16
#define pinDown  17
#define pinBite  19
#define pinDance 22



class SPIController {
  private:
    /** Class for handling button presses and storing for SPI communcation
     * This is saved as a bitfield, due to SPI interrupts needing to be very fast in accessing data
     */
    byte _state = 0;
    int  _refUp;
    int  _refLeft;
    int  _refRight;
    int  _refDown;
    int  _refBite;
    int  _refDance;

  public:

    /** Initialize all capacitive buttons so the threshhold is just above what the system boots with.
     *
     */

    SPIController() {
      _state = 0;

      _refUp 	= touchRead(pinUp) + 100;
      _refLeft = touchRead(pinLeft) + 100;
      _refRight = touchRead(pinRight) + 100;
      _refDown = touchRead(pinDown) + 100;
      _refBite = touchRead(pinBite) + 100;
      _refDance = touchRead(pinDance) + 100;
    }

    /**
     * Return the raw bitfield, which is usable as an SPI response
     */
    byte read() {
      return _state;
    }

    /*Functions for Marking a button as pressed*/
    void pressUp() {
      bitSet(_state, UP);
    }
    void pressDown() {
      bitSet(_state, DOWN);

    }
    void pressLeft() {
      bitSet(_state, LEFT);

    }
    void pressRight() {
      bitSet(_state, RIGHT);

    }
    void pressBite() {
      bitSet(_state, BITE);

    }
    void pressDance() {
      bitSet(_state, DANCE);

    }

    /*Functions for marking a button as released
     */
    void releaseUp() {
      bitClear(_state, UP);

    }
    void releaseDown() {
      bitClear(_state, DOWN);

    }
    void releaseLeft() {
      bitClear(_state, LEFT);

    }
    void releaseRight() {
      bitClear(_state, RIGHT);

    }
    void releaseBite() {
      bitClear(_state, BITE);

    }
    void releaseDance() {
      bitClear(_state, DANCE);

    }

    //read button states
    byte readUp() {
      return bitRead(_state, UP);
    }
    byte readDown() {
      return bitRead(_state, DOWN);

    }
    byte readLeft() {
      return bitRead(_state, LEFT);

    }
    byte readRight() {
      return bitRead(_state, RIGHT);

    }
    byte readBite() {
      return bitRead(_state, BITE);
    }
    byte readDance() {
      return bitRead(_state, DANCE);
    }

    /** Read all the button capacative values, and update pins appropriately
     */
    void update() {
      if (touchRead(pinUp) > _refUp) {
        pressUp();
      }
      else {
        releaseUp();
      }

      if (touchRead(pinDown) > _refDown) {
        pressDown();
      }
      else {
        releaseDown();
      }

      if (touchRead(pinLeft) > _refLeft) {
        pressLeft();
      }
      else {
        releaseLeft();
      }

      if (touchRead(pinRight) > _refRight) {
        pressRight();
      }
      else {
        releaseRight();
      }

      if (touchRead(pinBite) > _refBite) {
        pressBite();
      }
      else {
        releaseBite();
      }

      if (touchRead(pinDance) > _refDance) {
        pressDance();
      }
      else {
        releaseDance();
      }
    }


};



#endif

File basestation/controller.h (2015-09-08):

#ifndef CONTROLLER_H
#define CONTROLLER_H

#include <elapsedMillis.h>
#include <SPI.h>

/** Bit positions for sending button data over SPI
 *  X X UP DOWN LEFT RIGHT BITE DANCE
 */
#define UP 	5
#define DOWN 	4
#define LEFT 	3
#define RIGHT 	2
#define BITE 	1
#define DANCE 	0

struct Button {
  boolean pressed;         // true means pressed, false means not pressed
  boolean newValue;          // True if the button has not been read since last change
  elapsedMillis holdTime;  // time since button was last changed;
};


struct ControllerState {
  Button up;
  Button down;
  Button left;
  Button right;
  Button bite;
  Button dance;
};

class SPIController {
  private:
    byte _address;
    byte _ss_pin;
    elapsedMillis  _lastUpdate;
    ControllerState  _state;
    byte  _statebyte, _modified;

    ControllerState controller; //internal represenation of our button states


    // Private buttons which contain the button logic regarding new/read values. 
    boolean setButton(Button& button, boolean value) {
      if (button.pressed != value) {
        button.pressed = value;
        button.holdTime = 0;
        button.newValue = true;
        return true;
      }
      else {
        return false;
      }
    }

    boolean buttonUpdated(Button& button) {
        return button.newValue;

    }
    boolean buttonPressed(Button& button) {
          button.newValue=false;
          return button.pressed;
    }
   
    boolean buttonHeld(Button& button,int time) {
      return (button.pressed && (button.holdTime > time ) );
    }
    boolean buttonHeld(Button& button) {
       buttonHeld(button,200);
    }


  public:
    SPIController(byte address, int ss_pin) {
      _address = address;
      _ss_pin = ss_pin;

      digitalWrite (_ss_pin, HIGH);
      pinMode(_ss_pin, OUTPUT);
      SPI.begin();
    }


    ControllerState update() {
      if (_lastUpdate > 100) {
        _lastUpdate = 0;

        //Grab the data from the SPI bus
        //NOTE: The SPI speed may need to be adjusted, depending on the cabling and wire used.
        SPI.beginTransaction(SPISettings(2000000, MSBFIRST, SPI_MODE0));
        digitalWrite(_ss_pin, LOW);

        //We only need one byte, but the code is written for 2 for no particular reason
        //Stuff the outgoing data with the controller address
        byte msb = SPI.transfer(_address);
        byte lsb = SPI.transfer(0);

        //End by returning SS high
        digitalWrite(_ss_pin, HIGH);
        SPI.endTransaction();

        // do bit parsing and save to controllerstate
        setButton(controller.up,lsb & (1 << UP));
        setButton(controller.down,lsb & (1 << DOWN));
        setButton(controller.left,lsb & (1 << LEFT));
        setButton(controller.right,lsb & (1 << RIGHT));
        setButton(controller.dance,lsb & (1 << DANCE));
        setButton(controller.bite,lsb & (1 << BITE));
        
      }

      return _state;
    }
    
    boolean upPressed(){ return buttonPressed(controller.up);}
    boolean upUpdated(){ return buttonUpdated(controller.up);}
    boolean upHeld(){ return buttonHeld(controller.up);}

    boolean downPressed(){ return buttonPressed(controller.down);}
    boolean downUpdated(){ return buttonUpdated(controller.down);}
    boolean downHeld(){ return buttonHeld(controller.down);}

    boolean leftPressed(){ return buttonPressed(controller.left);}
    boolean leftUpdated(){ return buttonUpdated(controller.left);}
    boolean leftHeld(){ return buttonHeld(controller.left);}

    boolean rightPressed(){ return buttonPressed(controller.right);}
    boolean rightUpdated(){ return buttonUpdated(controller.right);}
    boolean rightHeld(){ return buttonHeld(controller.right);}

    boolean bitePressed(){ return buttonPressed(controller.bite);}
    boolean biteUpdated(){ return buttonUpdated(controller.bite);}
    boolean biteHeld(){ return buttonHeld(controller.bite);}

    boolean dancePressed(){ return buttonPressed(controller.dance);}
    boolean danceUpdated(){ return buttonUpdated(controller.dance);}
    boolean danceHeld(){ return buttonHeld(controller.dance);}
    
    
    byte debug(){
      return  controller.up.pressed << UP |
        controller.down.pressed << DOWN |
        controller.left.pressed << LEFT |
        controller.right.pressed << RIGHT |
        controller.dance.pressed << DANCE |
        controller.bite.pressed << BITE ;
    }
      
};

#endif

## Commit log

2015-08-09 V0, as built
    [base.brd, base.sch]
2015-08-24 Version 2 shark prototype boards
    [base.brd, base.sch]
2015-08-24 Added code and schematics for v1 of the land shark controller.
    [bottomlayer.gbl, bottommask.gbs, bottomsilk.gbo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]
2015-08-25 Move for better organization
    [base.brd, base.sch]
2015-08-25 Fixed silly silk. Moved trace. Changed LEFT and BOTTOM pins.
    [v2-landshark-handheld-controller.brd, v2-landshark-handheld-controller.sch]
2015-08-25 Added shark images to BITE and DANCE PARTY. Board file ready for gerberizing.
    [v2-landshark-handheld-controller.brd, v2-landshark-handheld-controller.sch]
2015-08-25 Made order. Added reference images. Added composite preview image. Added gerbers.
    [v2-landshark-handheld-controller.drills.xln]
2015-08-25 Moved traces to bottom layer. Added top ground plane with 40 mils isolation.
    [v2-landshark-handheld-controller.brd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]
2015-08-26 Preleminary layout for redoing in shark form factor
    [base.brd, base.sch]
2015-08-31 Added two mount holes, made board a little bigger, and added breakout power and SPI header.
    [v3-landshark-handheld-controller.brd, v3-landshark-handheld-controller.sch]
2015-09-01 Added v3 gerbers, final board. Added 7-pin breakout as per feeeeture creeeeep. Use the gerbers, I took some silk off the top layer.
    [v3-landshark-handheld-controller.brd, v3-landshark-handheld-controller.sch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]
2015-09-01 Just renaming folders.
    [bottomlayer.gbl, bottommask.gbs, bottomsilk.gbo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]
2015-09-01 Shark layout partly determined
    [base.brd, base.sch]
2015-09-01 Clean names for splitting files
    [brains.brd, brains.sch]
2015-09-01 Placement and LED routing complete
    [chassis.brd, chassis.sch]
2015-09-02 Updated routing and shuffled things a bit, tail
    [chassis.brd]
2015-09-02 Finished rerouting the brain board!
    [brains.brd, brains.sch]
2015-09-03 Fins mostly done, need panelizing
    [fins.brd, fins.sch]
2015-09-06 As ordered for Maker Faire
    [brains.brd, brains.sch, fins.brd]
2015-09-07 As-submitted pcb for controller-wifi basestation
    [basestation.brd, basestation.sch]
2015-09-07 SPI Now returns current state of buttons
2015-09-08 Button presses over wifi! :D
2015-09-08 Cleaned up organization a bit, cleaned filenames
    [basestation.brd, basestation.sch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]
2015-09-12 Bot code mostly working! Pre-MMF
    [brains.brd, brains.sch, chassis.brd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]
2015-09-13 DETECTING BUTTONS DANCING AND DOING THINGS
2015-11-17 Fixed layer issue that caused fab problem
    [brains.brd]
2015-11-17 Rename file structure for clarity
    [basestation.brd, basestation.sch, brains.brd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]
2015-11-21 Add hinge to part list
2015-11-23 Update button part number

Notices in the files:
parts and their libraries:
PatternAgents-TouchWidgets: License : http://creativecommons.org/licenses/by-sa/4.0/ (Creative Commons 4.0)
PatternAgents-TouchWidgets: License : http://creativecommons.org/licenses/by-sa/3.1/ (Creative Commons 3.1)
